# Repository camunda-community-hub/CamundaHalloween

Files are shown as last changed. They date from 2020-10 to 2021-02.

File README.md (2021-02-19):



# CamundaHalloween

It's a very Camunda Halloween, and this project should keep you safe from the
Trick-or-Treaters!

It's more than just a BPM process, of course. It's an IoT project that uses
Camunda BPM to deliver the goods.

I'll break this post up into several sections, but you will need (or at least need access to) a 3-D printer to fully realize the awesomness here. It uses a modified Dog Treat Dispenser because I didn't have the time (or the skills) to design a whole new Candy Dispenser from scratch.

## Overview

This is both a hardware and a software, as well as a BPMN, project, so there
are a lot of moving parts -- literally and figuratively.

The first thing I had to do was figure out what all those parts would be, and to map it all out.
Luckily, I had [Cawemo](https://www.https://cawemo.com) to get me started. I mapped out all the various parts of the
process there, and asked for feedback (because I could share the Cawemo model with some
collaborators!). Then, once I had the basic overall structure down, I moved it all over
to Camunda Modeler to flesh out the details of the process. This process of defining each
step in the process was very helpful in designing _all_ of the various parts.

So, here's the overall model I came up with (you can get the [complete file](Modeler/costume.bpmn) too):

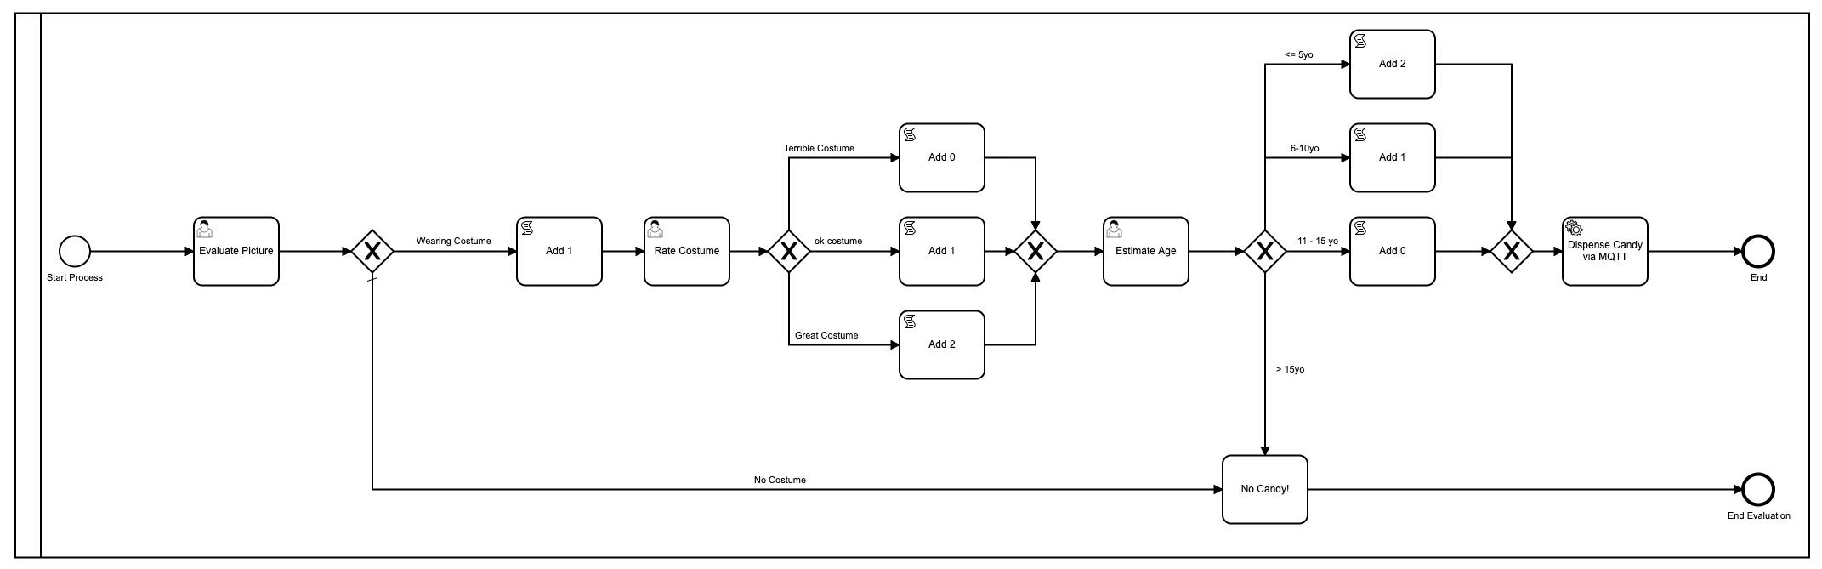
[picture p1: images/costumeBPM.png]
Halloween Candy Model


There are some areas where I could simplify things, of course, but this is, after all,
basically a [Rube Goldberg](https://en.wikipedia.org/wiki/Rube_Goldberg_machine) project of sorts,
so simplification wasn't really the goal. The basic steps are:
1. Trick-or-Treater rings doorbell
2. Camera takes a picture of the Trick-or-Treater and sends it to a server
3. User evaluates the picture to determine if the person is wearing a costume
   1. If they are not, they get no candy and the process ends
4. If they are, a piece of candy is added to their virtual candy bag
5. The picture is then evaluated a second time to judge the costume
   1. If the costume is really great, two pieces of candy are added to the virtual candy bag
   2. If the costume is just 'ok' one piece of candy is added
   3. If the costume is terrible, no additional candy is added
6. The picture is then evaluated a third time where the age of the Trick-or-Treater is determined
   1. If the Trick-or-Treater is 5 years old or under, they get two additional pieces of candy because little kids in cute costumes are the best
   2. If they are 6-10 years old, they get one additional piece of candy added
   3. If they are 11-15 years old, no additional candy is added
   4. If they are 15 years old or older, no candy will be dispensed and the process ends
7. All the candy is added up and sent to the automatic Candy Dispenser where the right number of pieces of candy are given out

Could I have made Halloween candy giving any more complicated? Probably. But I decided not to.

So there you have the overall layout. Next I needed to build the two pieces of hardware that
would allow me to make this dream come true. I needed a doorbell camera, and a treat dispenser.

For those things, I needed to build some custom hardware, and then 3-D print some custom pieces
to make it all come together.

I also had to write a small server process to take the pictures in from the Camera, and then
submit them to the Camunda Engine, as well as an external command that the Camunda Engine
could call at the end, which would start the candy being dispensed. I'll cover each of these
areas in its own section.

## 3-D Printing

With my printer, the printing took the better part of four days, so be prepared for some long days
watching your printer! I only printed the following parts from the included model:
* `treat-spout.stl` -- the spout where the treats come out!
* `hopper.stl` -- the hopper to hold your candy reserves
* `Screwll.stl` -- the screw that turns to dispense candy
* `feeder-tube.stl` -- the tube that the screw goes in
* `Hopper-lid.stl` -- the lid for the hopper

In addition, I did design and print one piece: `TreatHolder.stl` Since I didn't use a
servo motor, but instead opted to use stepper-motor, I had to design a part to hold
the stepper motor and the tube.

All of these files are in the `DispenserFiles` sub-directory. Happy printing!\

Depending on what motor you use to drive the screw, you _may_ have to customize the
hole just a bit to make the shaft fit.

Here's what the inside of the Dispenser looks like. You can see that it uses a screw-mechanism
to push candy along the tube.

Inside the Candy Dispenser

And when the whole thing is assembled and ready to dispense candy.

The completed candy dispenser

## The Hardware

I probably over-engineered this just a bit. :-) But there are essentially two different hardware builds here:
* Camera and Doorbell
* Treat Dispenser

I'll cover each of these separately, but none of the parts are hard to come by, and most,
if not all, should be available from [Adafruit](https://adafruit.com).

### The Camera and Doorbell

The camera and doorbell is based on the `ESP32-Cam` board which is a small, super cheap
board that has a fairly high quality camera on it. It's about 1" square (that's 2.5cm for those outside the US!)
and has an SD Card slot on it as well as a very bright flash. In addition, I added a momentary switch
(as the 'doorbell') and two LEDs -- a Green and a Red -- as status LEDs in case the board,
or the camera, don't come up correctly.

Here's how I wired it all up:

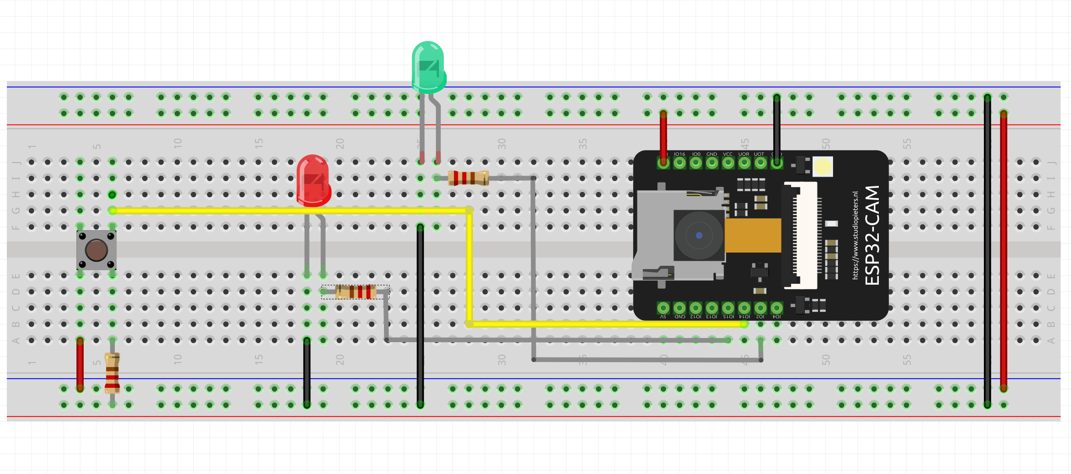
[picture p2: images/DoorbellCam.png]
Board Layout


And here's what the final product looks like:

Final Camera Board

My LEDs needed 100-Ohm resistors in order for them to get bright enough.
The doorbell has a 220-Ohm resistor on it. That's really all there is to it
for the wiring on the Doorbell/Camera side.

Now, on the Code side, there are a few things you'll need. You need to install
the ESP-32 Camera Library for Arduino, which you can get from the Espressif [GitHub](https://github.com/espressif/esp32-camera)
Once you have that, then the code in [CandyCam](CandyCam/CandyCam.ino) should
compile and work just fine.

**Note:** You will have to enter your WiFi SSID and Password on line `125` in order
to connect. You will also need to change the IP address of your server on line `204`.
These are hard-coded in order to save memory space as we are taking large pictures
on a small device.

### The Treat Dispenser

The Treat Dispenser uses a super-cheap Wemos D1 R2 Mini (ESP8266) D1. I buy them in bulk
for about US $1.50 each, so it's ok if they blow up now and then (they do). The Stepper
motor driver is an [Adafruit TB6612](https://www.adafruit.com/product/2448)which is about
US $5.00. The most expensive part of the whole thing is the [stepper motor](https://www.adafruit.com/product/324).

One part that is _not_ shown is the [boost step-up regulator](https://www.pololu.com/product/2117) that I used to bump the input voltage to the motor
from 3.3V to 12V

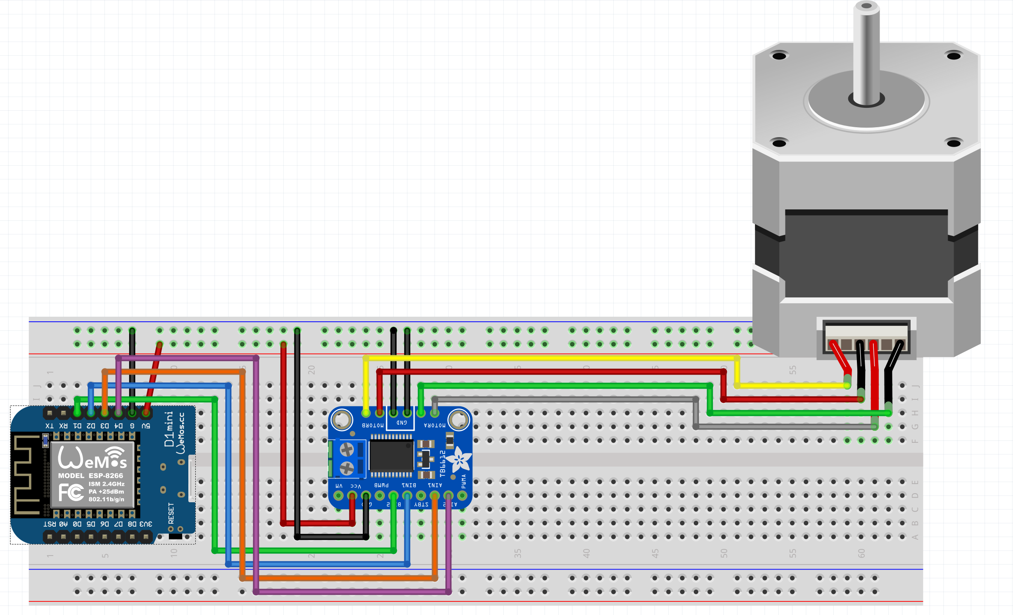
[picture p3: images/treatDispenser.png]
Treat Dispenser Wiring


And here's what that board looked like in its final form:

Treat Dispenser Final Circuit

Finally you'll need the code for the [Candy Dispenser](CandyDispenser/CandyDispenser.ino). Once again,
you'll need to make sure you set the address for your MQTT Broker (line `15`), your
WiFi access point and password (lines `24` & `25`).

## The Software

Now that you have all the hardware built and deployed, you need the software to pull it
all together and make it work. As mentioned before, when the 'doorbell' is pressed,
the Camera snaps a picture, stores it locally, and then sends it out. But where does it
send it?

### The Server Software

I originally tried to write the whole thing in JavaScript, but JavaScript has a memory
limit on incoming file sizes, so since I'm snapping fairly large pictures, I had to write
my own webserver, and I did that using Go.

The Webserver allows me to take in the picture files, stores them, and then serves them up
to the Camunda Task as needed. It also is responsible for initiating the task for each
new picture that comes in.

For that part, I used the Camunda [GoLang library](https://github.com/citilinkru/camunda-client-go).

```go
// sendPic sends the picture to the Camunda Process.
func sendPic(s string) {
	client := camundaclientgo.NewClient(camundaclientgo.ClientOptions{
		EndpointUrl: "http://localhost:8080/engine-rest",
		ApiUser:     "demo",
		ApiPassword: "demo",
		Timeout:     time.Second * 10,
	})
	newPath := prefix + strings.Trim(s, ".")
	processKey := "costumes"
	variables := map[string]camundaclientgo.Variable{
		"newCostume":  {Value: newPath, Type: "string"},
		"isCostume":   {Value: true, Type: "boolean"},
		"candyPieces": {Value: 0, Type: "long"},
	}
	_, err := client.ProcessDefinition.StartInstance(
		camundaclientgo.QueryProcessDefinitionBy{Key: &processKey},
		camundaclientgo.ReqStartInstance{Variables: &variables},
	)
	if err != nil {
		log.Printf("Error starting process: %s\n", err)
		return
	}
}
```
Notice that I'm setting all three process variables that I'll need throughout the entire
process here at the beginning. This was important for the `candyPieces` variable especially, 
since I found that if I tried to set it later on during the processs, it was defined as a
`double` and not a `long` which caused things not to work.

All of the code for the server process is included in [this project](GoServer/server.go) so
all you should have to do is run that file with the command `go run goserver.go` and you'll have
a webserver ready to take in pictures and start a Camunda Task in the Candy Dispenser!

### The Task Handler

This was the other piece I had to write: Something to handle the final task of dispensing
the right number of pieces of candy at the end. For this, I used Node.js, and the code
was just as simple:

```javascript
var mqtt = require('mqtt')
var mqttClient = mqtt.connect('mqtt://YOURBROKER')
const { Client, logger } = require('camunda-external-task-client-js');
const open = require('open');

// configuration for the Client:
//  - 'baseUrl': url to the Process Engine
//  - 'logger': utility to automatically log important events
//  - 'asyncResponseTimeout': long polling timeout (then a new request will be issued)
const config = { baseUrl: 'http://localhost:8080/engine-rest', use: logger, asyncResponseTimeout: 10000 };

// create a Client instance with custom configuration
const client = new Client(config);

client.subscribe('costumes', async function ({ task, taskService }) {

  candy = task.variables.get('candyPieces');
  console.log('Dispensing ' + candy + ' pieces of candy!');
  var cString = '{candy=' + candy + '}';
  mqttClient.publish('candy', cString);
  // Complete the task
  await taskService.complete(task);
});
```

In order to run this, run the following commands:
```sh
$ cd candy-dispenser-worker
$ npm install
$ node worker.js
```

## The Camunda Code

So now you should have a server process to take in the pictures and initiate a task,
and a service task worker to handle dispensing the code as the final task. It's time
to fill out all the parts of the model itself to make it fully functioning.

For the `Evaluate Picture` User Task, I created a form with two fields based on the
incoming task variables `isCostume` and `newCostume`.

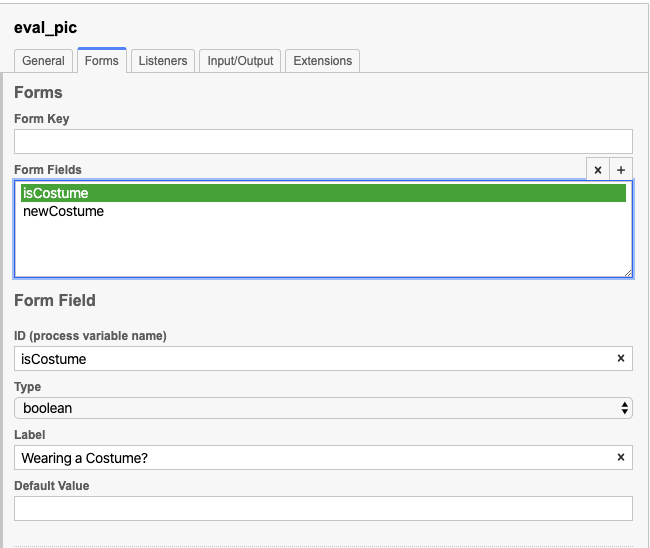
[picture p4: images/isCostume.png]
isCostume

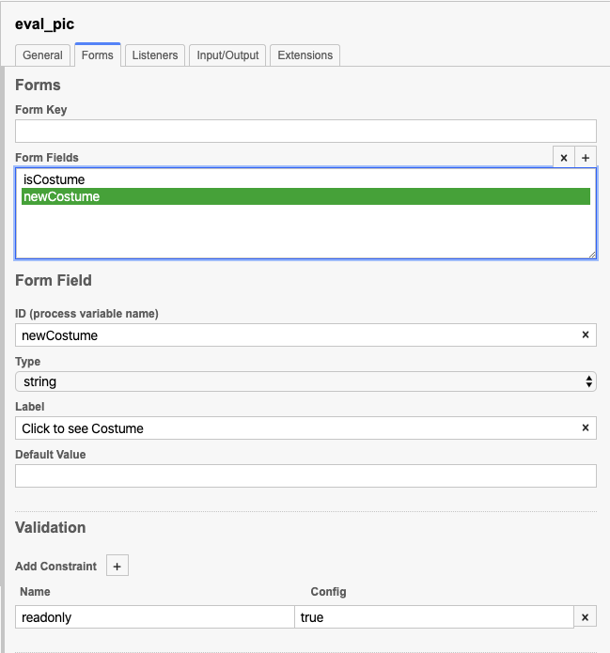
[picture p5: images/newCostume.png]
newCostume


I made the `newCostume` field `readonly` so that users couldn't accidentally go to the
wrong picture.

_Area for improvement:_ Making the picture link in the form actually
clickable rather than having the user copy/paste the link into a new browser window.

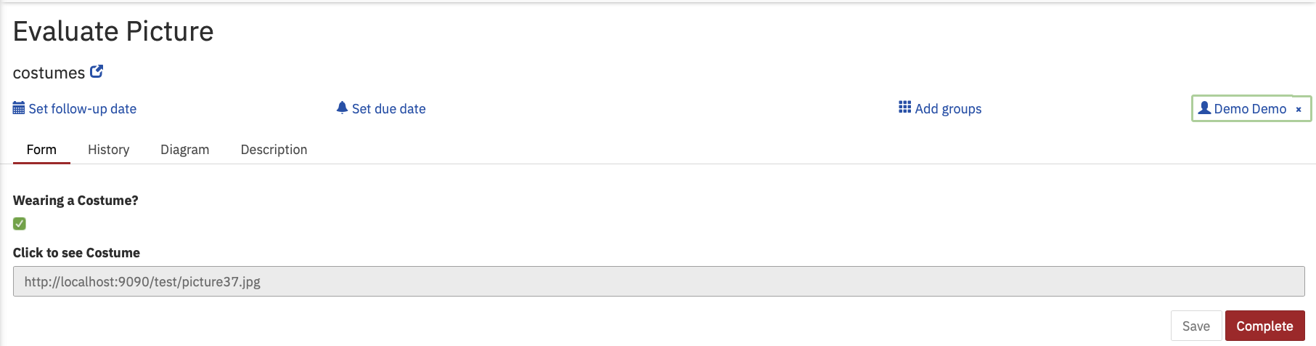
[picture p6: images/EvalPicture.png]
Evaluate the Picture


The process then adds a single piece of candy to the virtual candy bag, and for this
I used a Script Task with a small bit of javascript code:

```javascript
var candy = execution.getVariable('candyPieces');
if(candy == null){
   candy = 0;
}
candy += 1;
execution.setVariable('candyPieces', candy);
```

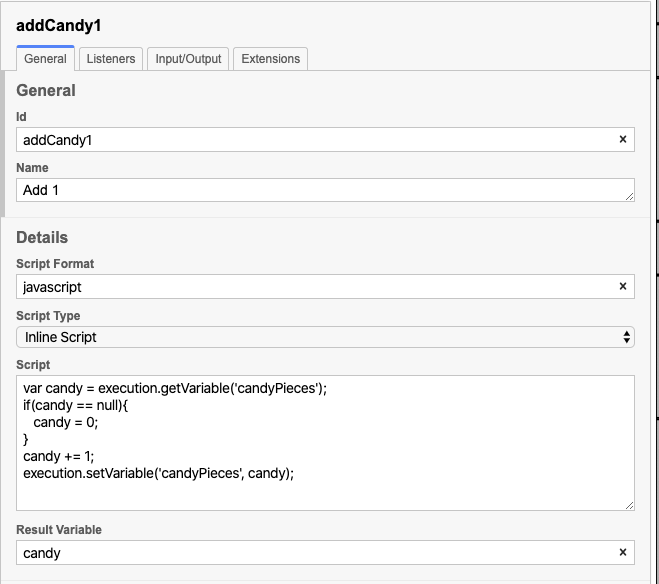
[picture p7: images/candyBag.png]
Candy Code


I'm using the global `candyPieces` variable that we set way back in the web server code
to keep track of the amount of candy.

Once we've done that, it's time to Rate the Costume, so I made another form:

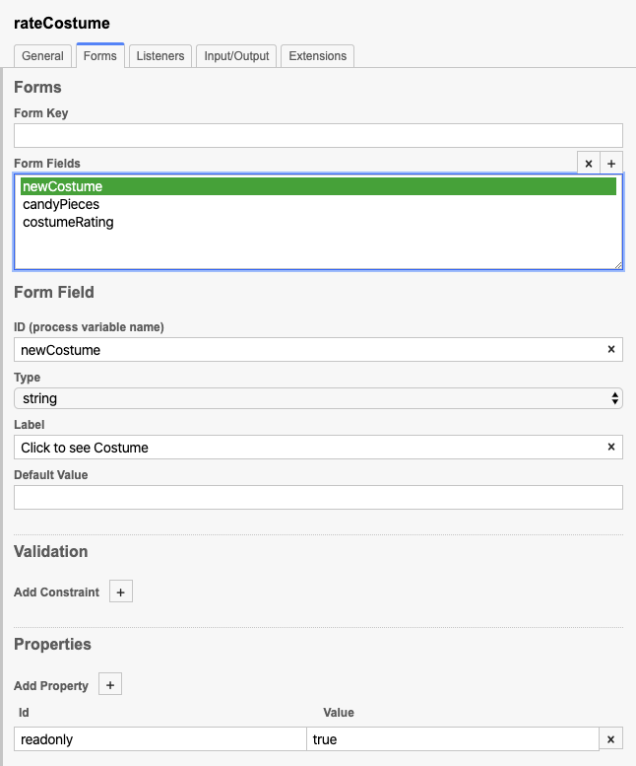
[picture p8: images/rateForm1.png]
Rate Form 1

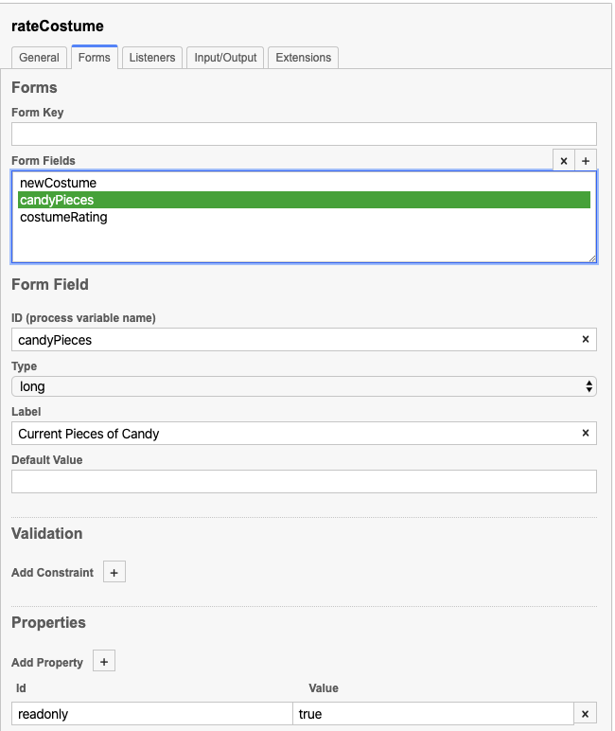
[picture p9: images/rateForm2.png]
Rate Form 2

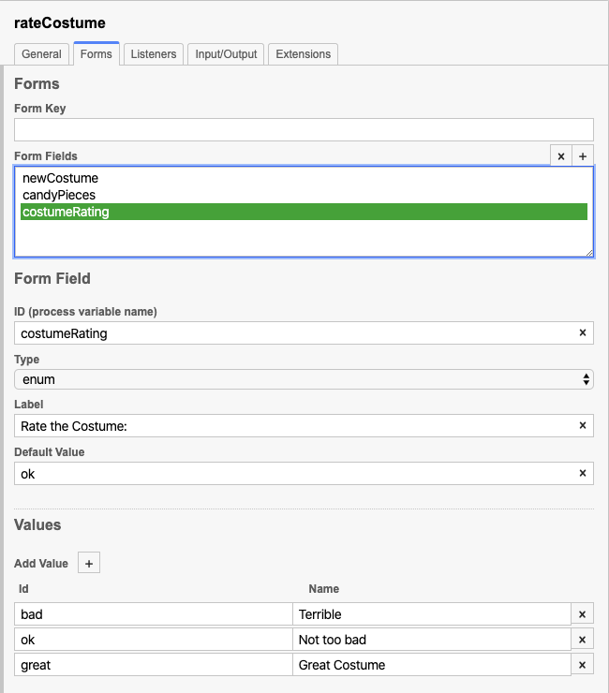
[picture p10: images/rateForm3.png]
Rate Form 3


Again, the number of pieces of candy is not editable, because we don't want anyone cheating!

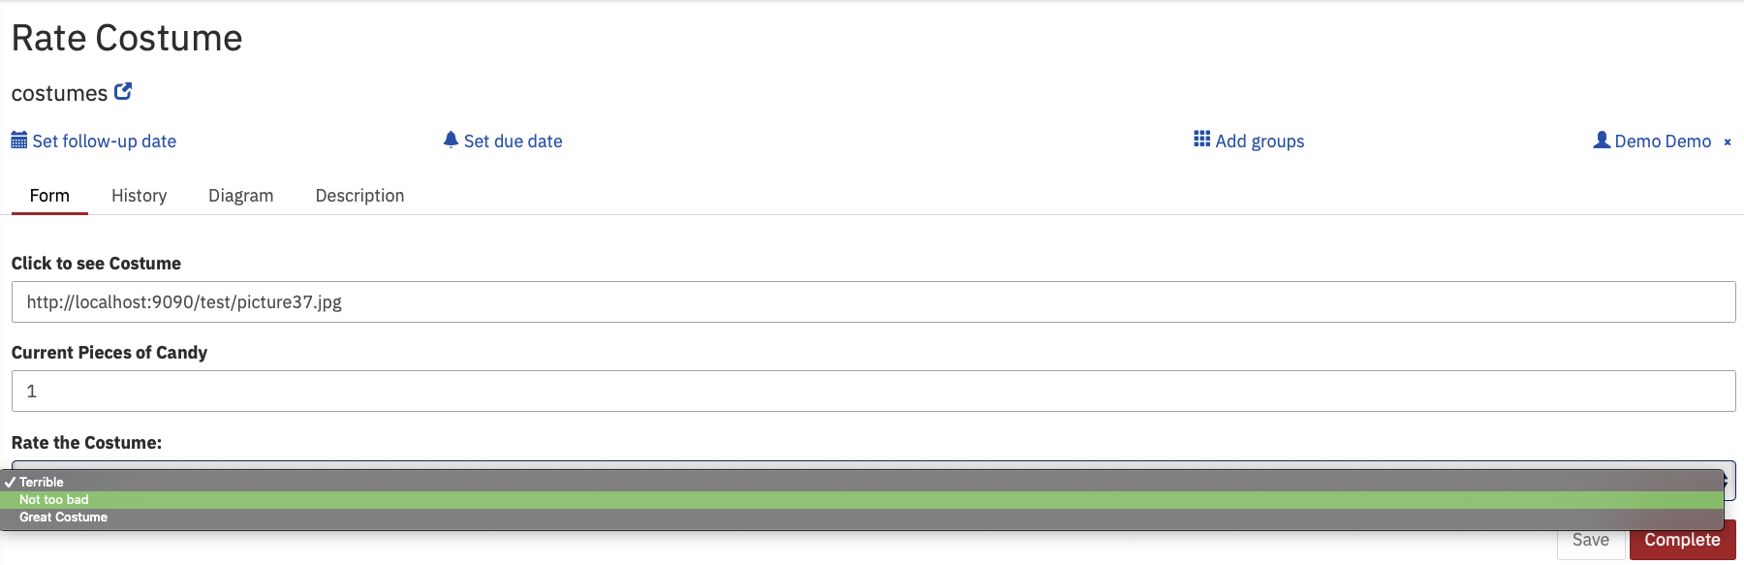
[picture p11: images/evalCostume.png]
Rate the Costume


After this I needed to add more candy to the count (maybe, unless they had a
terrible costume) so I re-used the javascript code from the first Script Task for
all of the rest of them, just adjusting the amount (if any) of candy to be added.

And finally we estimate the Trick-or-Treater's age:

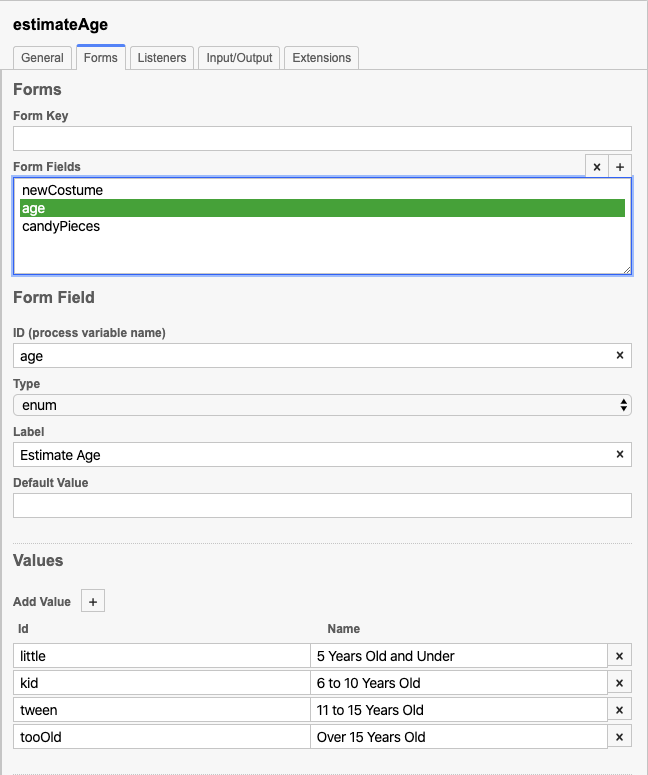
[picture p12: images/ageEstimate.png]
Age Estimation Form


Which turns into a nice form:

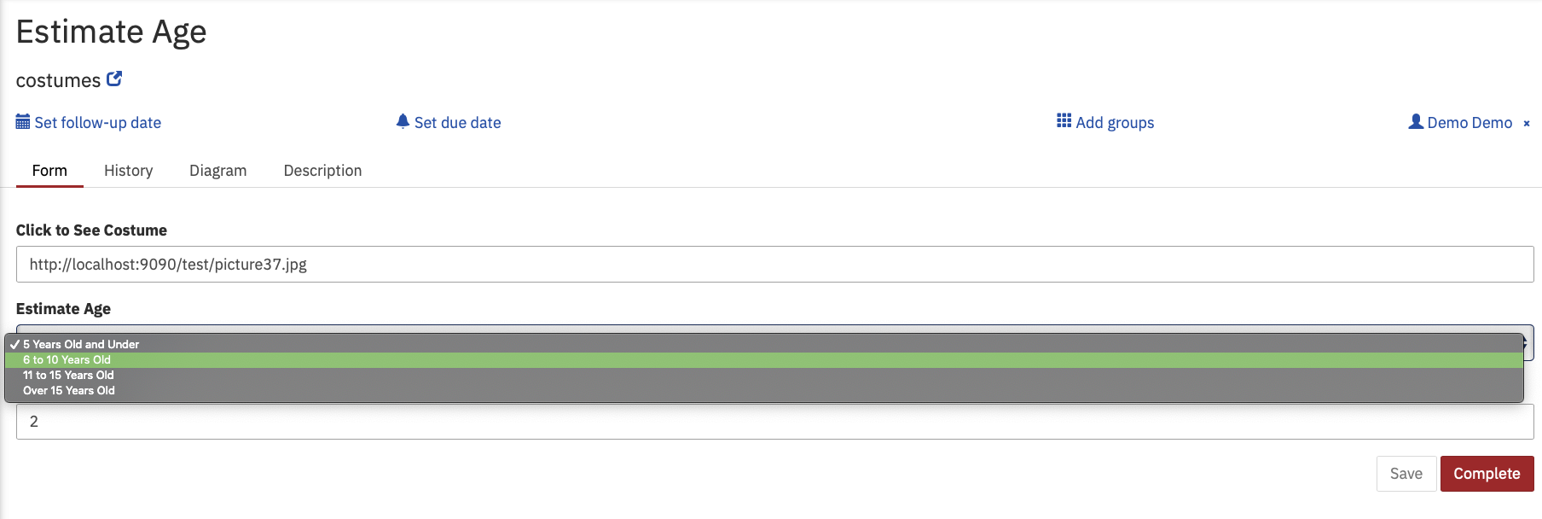
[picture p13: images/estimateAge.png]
Estimate age


And once again re-use the javascript for the Script Tasks to add candy to the
candy bag.

The final step is to send the whole thing off to the worker task we defined earlier:

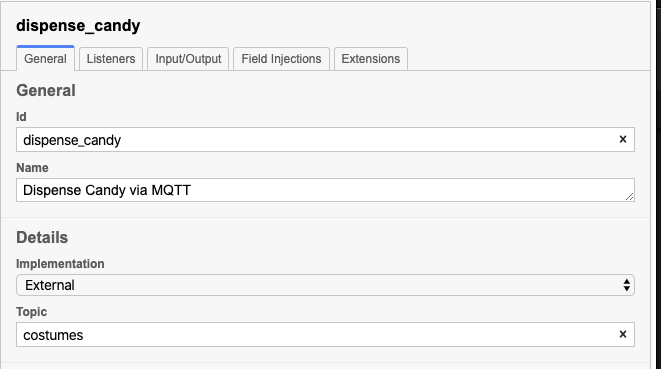
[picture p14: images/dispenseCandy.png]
Dispense Candy!


Notice that I set the `topic` to the same thing as I defined as my `topic` in the
`worker.js` file previously. When a task is completed, you should see the
following in the console where you started that task:

```bash
% node ./worker.js
✓ subscribed to topic costumes
Dispensing 4 pieces of candy!
✓ completed task ca3ae72e-1875-11eb-82d1-0242ac110002
```

Which indicates that the candy was dispensed, and the task was completed!

Success!!

## Conclusions

I was asked more than a few times how BPMN and IoT could ever be a 'thing' together,
and I was fully prepared for the answer to be "it can't".

But then I got to thinking about it -- there are actually thousands of ways in
which IoT data from sensors, etc. can be key pieces of data in a business decision-making
process.

In addition, having the ultimate outcome of a business-decision-making process be something
that is then carried out in the physical world -- maybe it's a treat dispenser, but
maybe it's a warehouse robot that is tasked to go collect and process an order -- is a
very real need.

So while I may have proven that BPMN and IoT can go together in the very dumbest way
possible, it was a super fun project, and I hope it gets you thinking about other
possibilities either for you IoT project, or for your BPMN processes.

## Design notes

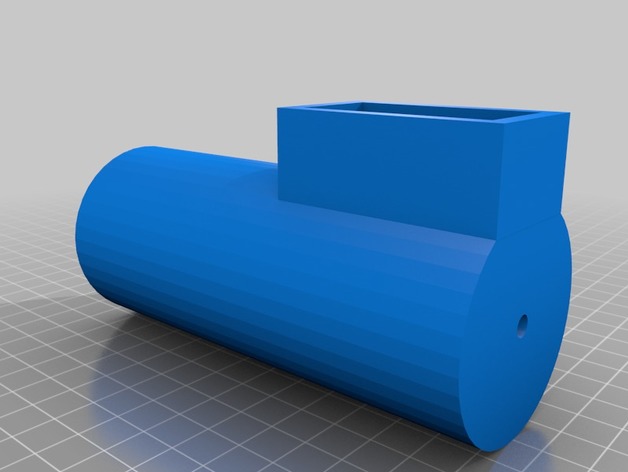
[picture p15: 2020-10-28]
DispenserFiles/Dog_Treat_Dispenser/images/704567c27d15f55ea5f7be787164375c_preview_featured.jpg

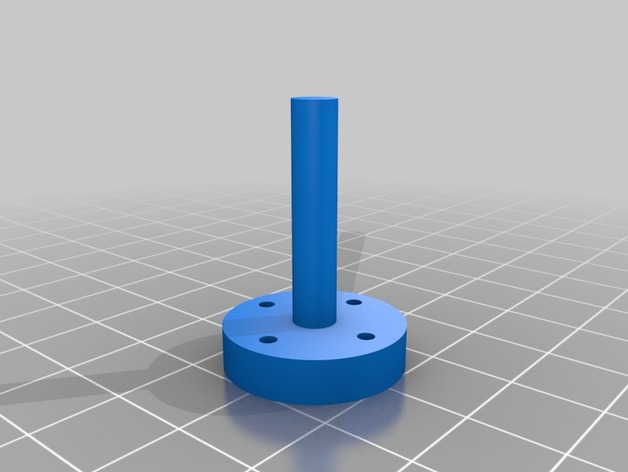
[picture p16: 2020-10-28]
DispenserFiles/Dog_Treat_Dispenser/images/bddad45c9091de8ab5bde2026ed623f4_preview_featured.jpg

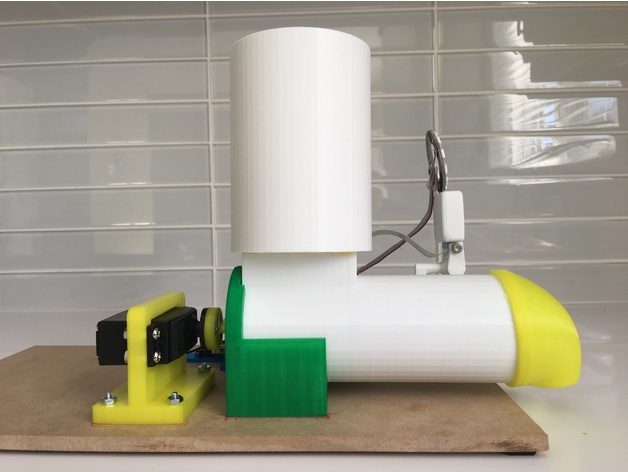
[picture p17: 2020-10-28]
DispenserFiles/Dog_Treat_Dispenser/images/47451cfe895809430f1f28f30e1b4cd2_preview_featured.JPG

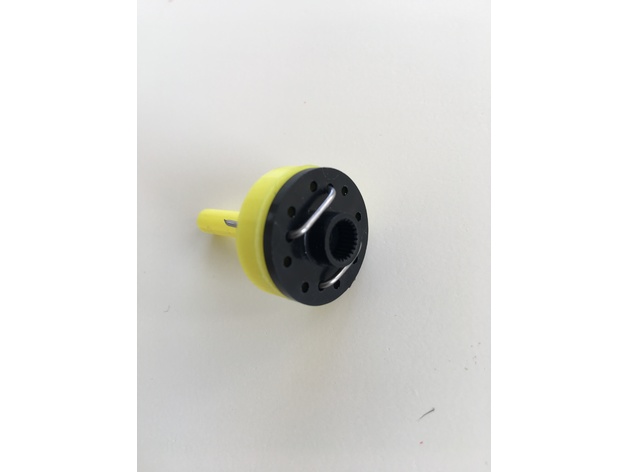
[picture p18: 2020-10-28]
DispenserFiles/Dog_Treat_Dispenser/images/afd8b5390522d9ebc6c4b27319f96526_preview_featured.JPG

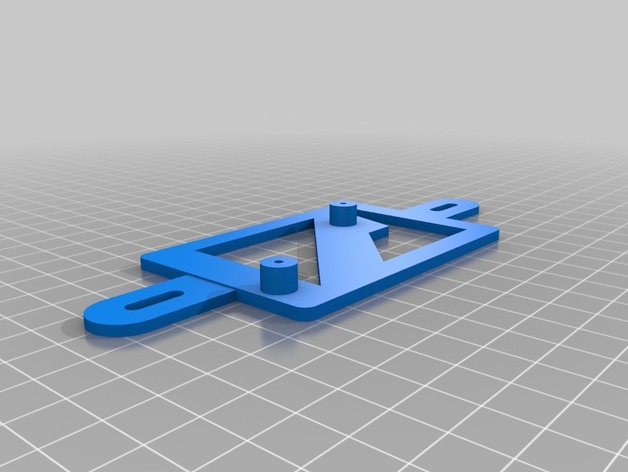
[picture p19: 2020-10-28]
DispenserFiles/Dog_Treat_Dispenser/images/8374462ad5bfc6478ba845c1a7bec97a_preview_featured.jpg

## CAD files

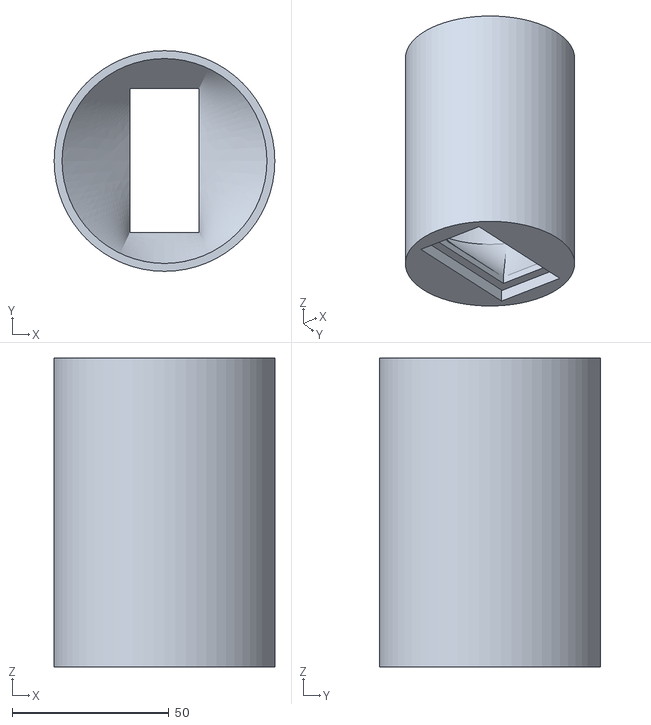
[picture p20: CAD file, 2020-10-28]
DispenserFiles/Dog_Treat_Dispenser/files/hopper.stl
70.3 x 70.3 x 98.5

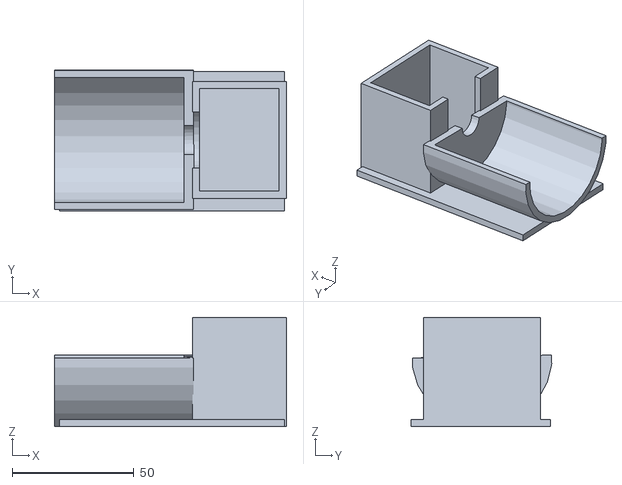
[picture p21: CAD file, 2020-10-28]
DispenserFiles/TreatHolder.stl
95.5 x 57.8 x 45.0

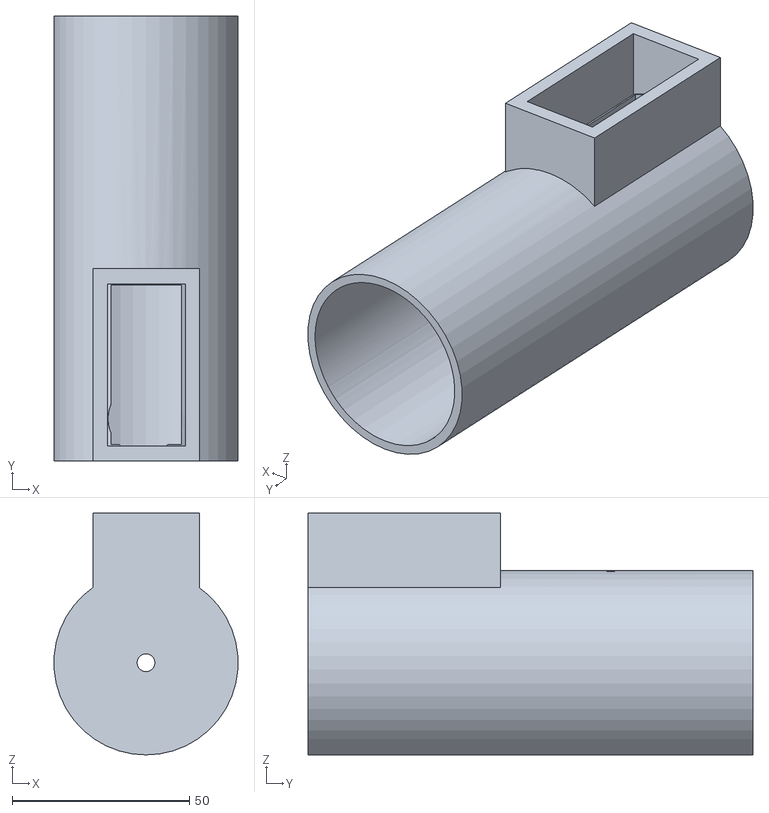
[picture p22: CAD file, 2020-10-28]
DispenserFiles/Dog_Treat_Dispenser/files/feeder-tube.stl
51.9 x 125.6 x 68.2

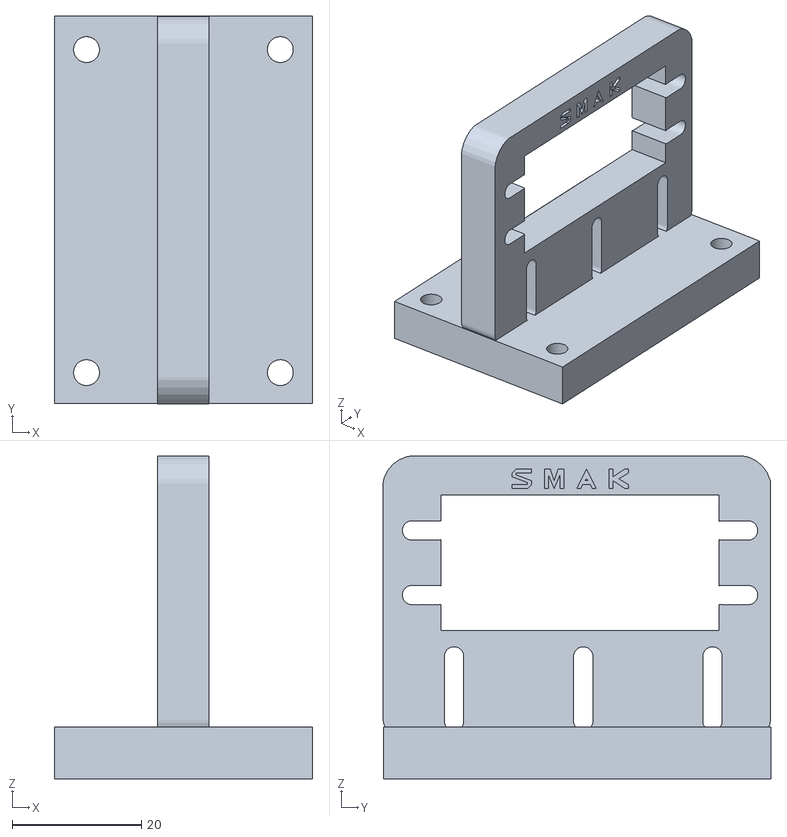
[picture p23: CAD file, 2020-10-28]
DispenserFiles/Dog_Treat_Dispenser/files/servostand.stl
40.0 x 60.1 x 49.9

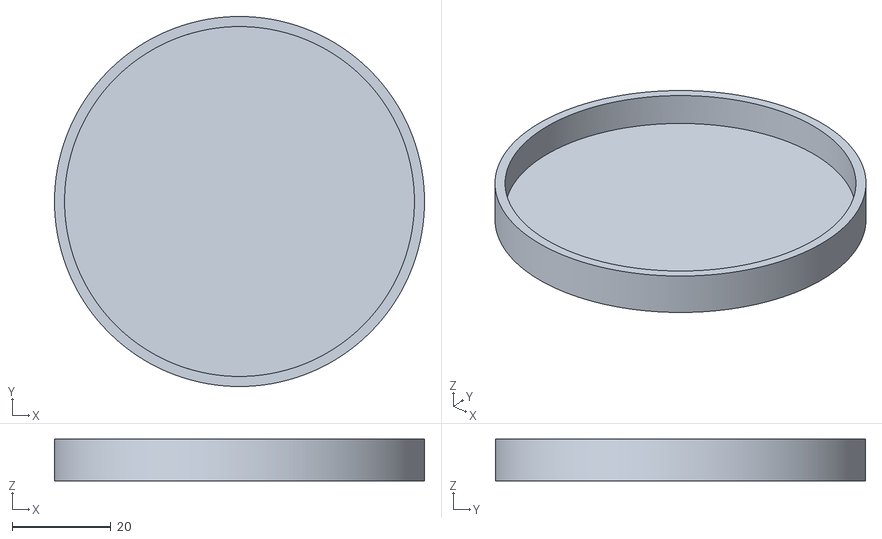
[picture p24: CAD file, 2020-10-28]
DispenserFiles/Dog_Treat_Dispenser/files/Hopper-Lid.stl
75.0 x 75.0 x 8.50

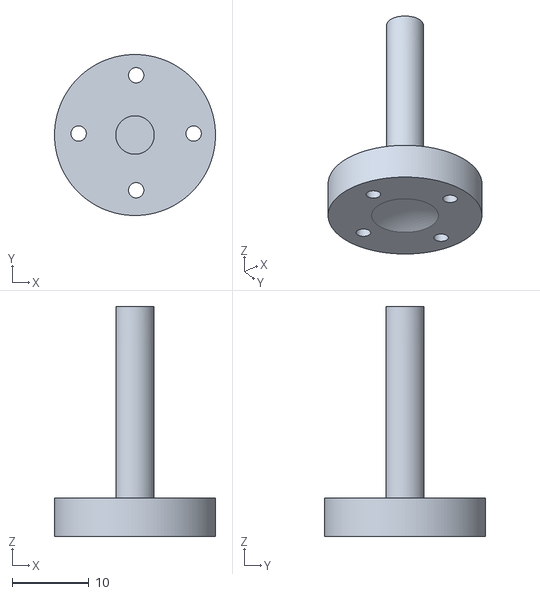
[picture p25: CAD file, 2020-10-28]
DispenserFiles/Dog_Treat_Dispenser/files/servocoupler.stl
21.0 x 21.0 x 30.0

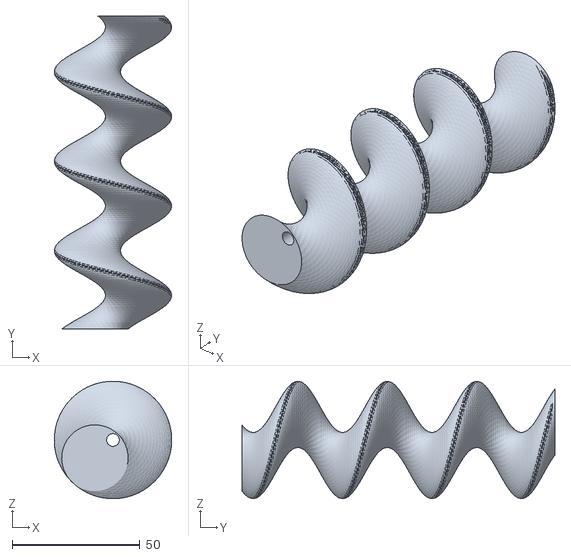
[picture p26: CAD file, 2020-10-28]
DispenserFiles/Dog_Treat_Dispenser/files/ScrewII.STL
46.0 x 122.5 x 46.0

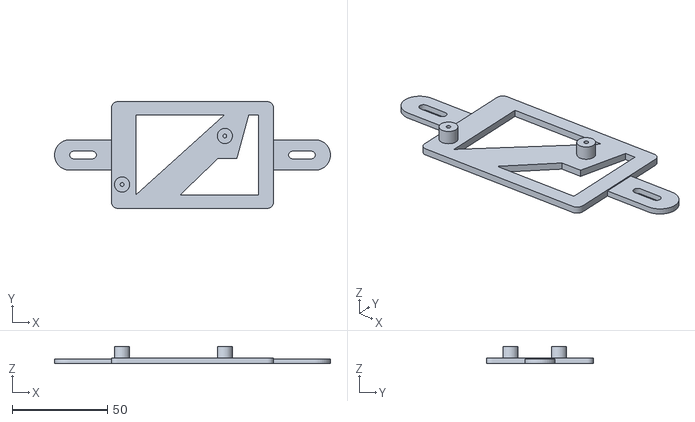
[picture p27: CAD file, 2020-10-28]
DispenserFiles/Dog_Treat_Dispenser/files/raspberrypi_plate_screwmount.stl
145.0 x 56.0 x 9.00

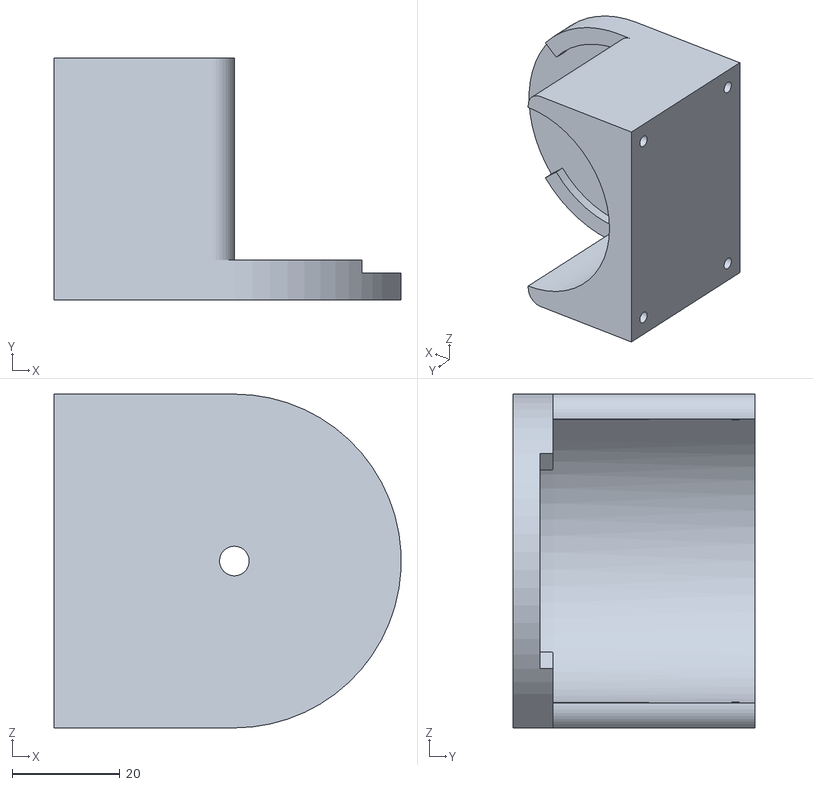
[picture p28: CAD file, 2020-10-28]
DispenserFiles/Dog_Treat_Dispenser/files/Screw_Motor_Mount.STL
64.5 x 45.0 x 62.0

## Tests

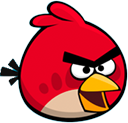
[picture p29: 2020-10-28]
GoServer/test/angry-bird.png

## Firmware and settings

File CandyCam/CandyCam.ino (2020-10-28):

#include "esp_camera.h"
#include <WiFi.h>
#include <HTTPClient.h>
#include "FS.h"               // SD Card ESP32
#include "SD_MMC.h"           // SD Card ESP32
#include "soc/soc.h"          // Disable brownout problems
#include "soc/rtc_cntl_reg.h" // Disable brownout problems
#include "driver/rtc_io.h"
#include <EEPROM.h> // read and write from flash memory
#include "camera_pins.h"
//
// WARNING!!! Make sure that you have either selected ESP32 Wrover Module,
//            or another board which has PSRAM enabled
//

#define CAMERA_MODEL_AI_THINKER
#define EEPROM_SIZE 1
#define REDLED 15
#define GREENLED 13

WiFiClient client;
int pictureNumber = 0;
void setup()
{
  WRITE_PERI_REG(RTC_CNTL_BROWN_OUT_REG, 0);
  Serial.begin(115200);
  // Serial.setDebugOutput(true);
  pinMode(4, OUTPUT);
  pinMode(14, INPUT);
  pinMode(REDLED, OUTPUT);
  pinMode(GREENLED, OUTPUT);
  digitalWrite(REDLED, LOW);
  digitalWrite(GREENLED, LOW);
  int z = 0;
  while (z < 20)
  {
    digitalWrite(GREENLED, HIGH);
    delay(250);
    digitalWrite(GREENLED, LOW);
    digitalWrite(REDLED, HIGH);
    delay(250);
    digitalWrite(REDLED, LOW);
    z++;
  }
  //digitalWrite(lampledPin, HIGH);
  camera_config_t config;
  config.ledc_channel = LEDC_CHANNEL_0;
  config.ledc_timer = LEDC_TIMER_0;
  config.pin_d0 = Y2_GPIO_NUM;
  config.pin_d1 = Y3_GPIO_NUM;
  config.pin_d2 = Y4_GPIO_NUM;
  config.pin_d3 = Y5_GPIO_NUM;
  config.pin_d4 = Y6_GPIO_NUM;
  config.pin_d5 = Y7_GPIO_NUM;
  config.pin_d6 = Y8_GPIO_NUM;
  config.pin_d7 = Y9_GPIO_NUM;
  config.pin_xclk = XCLK_GPIO_NUM;
  config.pin_pclk = PCLK_GPIO_NUM;
  config.pin_vsync = VSYNC_GPIO_NUM;
  config.pin_href = HREF_GPIO_NUM;
  config.pin_sscb_sda = SIOD_GPIO_NUM;
  config.pin_sscb_scl = SIOC_GPIO_NUM;
  config.pin_pwdn = PWDN_GPIO_NUM;
  config.pin_reset = RESET_GPIO_NUM;
  config.xclk_freq_hz = 20000000;
  config.pixel_format = PIXFORMAT_JPEG;
  //init with high specs to pre-allocate larger buffers
  if (psramFound())
  {
    //  Serial.println("Getting XGA Images");
    config.frame_size = FRAMESIZE_XGA;
    config.jpeg_quality = 10;
    config.fb_count = 2;
  }
  else
  {
    Serial.println("Stuck with SVGA");
    config.frame_size = FRAMESIZE_SVGA;
    config.jpeg_quality = 12;
    config.fb_count = 1;
  }

#if defined(CAMERA_MODEL_ESP_EYE)
  pinMode(13, INPUT_PULLUP);
  pinMode(14, INPUT_PULLUP);
#endif

  // camera init
  esp_err_t err = esp_camera_init(&config);
  if (err != ESP_OK)
  {
    Serial.printf("Camera init failed with error 0x%x", err);
    flashError();
  }
  if (!SD_MMC.begin())
  {
    Serial.println("SD Card Mount Failed");
    flashError();
  }

  uint8_t cardType = SD_MMC.cardType();
  if (cardType == CARD_NONE)
  {
    Serial.println("No SD Card attached");
    flashError();
  }

  sensor_t *s = esp_camera_sensor_get();
  //initial sensors are flipped vertically and colors are a bit saturated
  if (s->id.PID == OV3660_PID)
  {
    s->set_vflip(s, 1);       //flip it back
    s->set_brightness(s, 1);  //up the blightness just a bit
    s->set_saturation(s, -2); //lower the saturation
  }
  //drop down frame size for higher initial frame rate
  s->set_framesize(s, FRAMESIZE_XGA);

#if defined(CAMERA_MODEL_M5STACK_WIDE)
  s->set_vflip(s, 1);
  s->set_hmirror(s, 1);
#endif

  WiFi.begin("YOURSSID", "YOUR_WIFI_PASSWD");

  while (WiFi.status() != WL_CONNECTED)
  {
    delay(500);
    Serial.print(".");
  }
  Serial.println("\nWiFi connected");

  EEPROM.begin(EEPROM_SIZE);
  pictureNumber = EEPROM.read(0) + 1;

  Serial.print("Camera Ready!");
  digitalWrite(GREENLED, HIGH);
}

void flashError()
{
  while (1)
  {
    digitalWrite(REDLED, HIGH);
    delay(500);
    digitalWrite(REDLED, LOW);
  }
}
void loop()
{
  if (digitalRead(14) == HIGH)
  {

    digitalWrite(4, HIGH);
    camera_fb_t *fb = NULL;
    delay(1000);
    fb = esp_camera_fb_get();
    if (!fb)
    {
      Serial.println("Camera capture failed");
      digitalWrite(GREENLED, LOW);
      int x = 10;
      while (x > 0)
      {
        digitalWrite(REDLED, HIGH);
        delay(500);
        digitalWrite(REDLED, LOW);
        x--;
      }
      digitalWrite(GREENLED, HIGH);
      return;
    }
    String path = "/picture" + String(pictureNumber) + ".jpg";
    fs::FS &fs = SD_MMC;
    // Serial.printf("Picture file name: %s\n", path.c_str());
    while (fs.exists(path.c_str()))
    {
      Serial.printf("File %s exists, incrementing...", path.c_str());
      pictureNumber++;
      path = "/picture" + String(pictureNumber) + ".jpg";
    }
    File file = fs.open(path.c_str(), FILE_WRITE);
    if (!file)
    {
      Serial.println("Failed to open file in writing mode");
    }
    else
    {
      file.write(fb->buf, fb->len); // payload (image), payload length
      Serial.printf("Saved file to path: %s\n", path.c_str());
      EEPROM.write(0, pictureNumber);
      EEPROM.commit();
    }
    file.close();
    digitalWrite(4, LOW);

    file = fs.open(path.c_str(), FILE_READ);
    String fileName = file.name();
    String fileSize = String(file.size());

    if (file)
    {
      byte server[] = {192, 168, 1, 213};
      if (client.connect(server, 9090))
      {
        Serial.println(F("connected to server"));

        //      // Make a HTTP request:
        //
        String start_request = "";
        String end_request = "";
        start_request = start_request +
                        "\n--AaB03x\n" +
                        "Content-Disposition: form-data; name=\"uploadfile\"; filename=\"" + file.name() + "\"\n" +
                        "Content-Transfer-Encoding: binary\n\n";
        String midRequest = "";
        midRequest += "\n--AaB03x\nContent-Disposition: form-data; foo=\"bar\"; \nContent-Transfer-Encoding: text\n\n";
        end_request = end_request + "\n--AaB03x--\n";
        uint16_t full_length;
        full_length = start_request.length() + file.size() + midRequest.length() + end_request.length();
        Serial.println("Connected ok!");
        client.println("POST /photo HTTP/1.1");
        client.println("Host: example.com");
        client.println("User-Agent: ESP32");
        client.println("Content-Type: multipart/form-data; boundary=AaB03x");
        client.print("Content-Length: ");
        client.println(full_length);
        client.print(start_request);
        const int bufSize = 2048;
        byte clientBuf[bufSize];
        int clientCount = 0;
        while (file.available())
        {
          clientBuf[clientCount] = file.read();
          clientCount++;
          if (clientCount > (bufSize - 1))
          {
            client.write((const uint8_t *)clientBuf, bufSize);
            // Serial.print((char *)clientBuf);
            clientCount = 0;
          }
        }
        if (clientCount > 0)
        {
          client.write((const uint8_t *)clientBuf, clientCount);
          // Serial.print((char *)clientBuf);
        }
        client.print(midRequest);
        client.print(end_request);
        client.stop();
        Serial.println("Done!");

        esp_camera_fb_return(fb);
      }
    }
  }
}

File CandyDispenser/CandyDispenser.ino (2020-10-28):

#include <ESP8266WiFi.h>
//needed for library
#include <DNSServer.h>
#include <ESP8266WebServer.h>
#include <WiFiManager.h>
#include <PubSubClient.h>
#include <Adafruit_NeoPixel.h>
#include <ESP8266mDNS.h>
#include <WiFiUdp.h>
#include <Stepper.h>

// change this to the number of steps on your motor
#define STEPS 200
#define CANDY 200
#define BROKER "YOUR-BROKER"
#define CLIENTID "CandyMan"
#define COMMAND_TOPIC "candy"
#define PASSWORD ""
// create an instance of the stepper class, specifying
// the number of steps of the motor and the pins it's
// attached to
Stepper stepper(STEPS, D4, D3, D2, D1);

const char *ssid = "YOURSSID";
const char *password = "YOURPASSWORD";
int status = WL_IDLE_STATUS; // the Wifi radio's status
WiFiClient espClient;
PubSubClient client(espClient);

void setup()
{
  Serial.begin(115200);
  Serial.println("Stepper test!");
  // set the speed of the motor to 30 RPMs
  stepper.setSpeed(60);
  WiFi.begin(ssid, password);

  while (WiFi.status() != WL_CONNECTED)
  {
    delay(500);
    Serial.print(".");
  }
  Serial.println("");
  Serial.println("WiFi connected");
  client.setServer(BROKER, 8883);
  client.setCallback(callback);
}

int wait_for_wifi()
{
  int tries = 30;
  int thisTry = 0;
  Serial.println("waiting for Wifi");
  while (WiFi.status() != WL_CONNECTED && thisTry < tries)
  {
    delay(1000);
    thisTry += 1;
  }
  if (WiFi.status() != WL_CONNECTED)
  {
    return 1;
  }
  Serial.println("");
  Serial.println("WiFi connected");
  return 0;
}

void reconnect()
{
  boolean first = true;
  // Loop until we're reconnected to the broker
  while (!client.connected())
  {
    if (WiFi.status() != WL_CONNECTED)
    {
      wait_for_wifi();
      first = true;
    }
    // Attempt to connect
    if (client.connect(CLIENTID, "use-token-auth", PASSWORD))
    {
      Serial.println("connected");
    }
    else
    {
      Serial.print("failed, rc=");
      Serial.println(client.state());
    }
  }
  // subscribe to the command topic
  client.subscribe(COMMAND_TOPIC);
}

void callback(char *topic, byte *payload, unsigned int length)
{
  String s = String((char *)payload);
  s.trim();
  // "+1" to skip over the '{'
  s = s.substring(s.indexOf("=") + 1, s.lastIndexOf("}"));
  s.trim();
  int c = s.toInt();
  Serial.print("Dispensing ");
  Serial.print(c);
  Serial.println(" pieces of candy.");
  int t = c * CANDY;
  Serial.println(t);
  for (int x = 0; x < c; x++)
  {
    stepper.step(-CANDY);
  }
  Serial.println("Done!");
}

void loop()
{
  if (!client.connected())
  {
    reconnect();
  }
  client.loop();
}
